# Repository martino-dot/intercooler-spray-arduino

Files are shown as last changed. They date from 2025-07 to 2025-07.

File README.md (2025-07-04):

# Intercooler Spray Arduino
A program for the Arduino Due that lets it control an intercooler sprayer in a Subaru STi. 

Intended setup is a developmental board on top of the Arduino to house a transistor that controls the incandescent bulb on the intercooler spray switch for feedback, and 3.3v relay board to control the pump. 

## Features
* Adjustable auto intercooler spray
* Can spray under boost, on a set interval, or manually
* Saves spray mode through power loss
* Cooldown spray
* Low water level warning and auto disable when level is low
* Refill detection and feedback
* Diagnostic features

## Required Dependencies
[DueFlashStorage](https://github.com/sebnil/DueFlashStorage)

## Pin Assignments
**Digital Pin 3** - Status LED Output (Linked to the Intercooler Spray Button Bulb)

**Digital Pin 5** -Low Level Sensor Input (Normally closed)

**Digital Pin 6** - Intercooler Spray Button Input (Or any other momentary button; Normally Open)

**Digital Pin 7** - HOBBs Switch Input (Used to determine if in boost; Normally Open)

**Digital Pin 8** -  Pump Relay Output

## Default parameters
**Single Button Press** - Whenever under boost, sprays for 2 seconds every 30 seconds. A cooldown spray is sprayed whenever car is under boost for more than 20 seconds in a 1 minute window.

**Double Button Press** - Sprays for 2 seconds every 30 seconds, regardless of boost. No boost tracking.

**Button Held Down** - If the button is held down for more than 2 seconds a *forced* spray will run, regardless of what mode it is in, until the button is let go. If water is low level, then this mode will NOT turn on and the status light will blink rapidly instead.

**Turning a Mode off** - Pressing the button **once** in a mode will turn it off.

**Switching Modes** - You **must** disable one of the modes before activating the other. 

**Additional Note** - Modes WILL be saved when the car is turned off and then back on. However, during startup delay, no mode will spray any water until it is done. If the water level is LOW then the mode will automatically be put into off.

**Startup Delay** - There is a 15 second delay before being able to control anything when turning the arduino/car on. During startup the status LED will blink once to signify for boost mode, blink twice for interval mode, and blink rapidly for low water, otherwise it will stay off.

**LED Status Blinks:**

&nbsp;&nbsp;1 Blink - Boost mode is ON

&nbsp;&nbsp;2 Blinks - Interval Mode is ON

&nbsp;&nbsp;3 Blinks - Mode 1 or 2 is turned off

&nbsp;&nbsp;5 Blinks - Tank Refilled

&nbsp;&nbsp;Rapid Blinks - Low Water Level

&nbsp;&nbsp;Constant On - Forced mode is running

## Diagnostics
When connected to the Arduino through the **programming USB port**, in serial console the following commands will report the following information:

&nbsp;&nbsp;**p** - Pump Relay Test (turns on pump for 1 second)

&nbsp;&nbsp;**l** - Status LED test (turns on LED for 1 second)

&nbsp;&nbsp;**w** - Checks water level

&nbsp;&nbsp;**m** - Lets you switch between modes (off, boost, and interval)

&nbsp;&nbsp;**d** - Reports current mode, time since last spray, and water status (Available after startup delay)

&nbsp;&nbsp;**r** - Restarts arduino

## 3D Models
I've included the 3D model for the intercooler box and intercooler box cap. It is designed to fit an Arduino Due, a single 3.3v relay module, and a development board on top of the arduino. The Arduino should sit on the side with the text engraved, so the programming USB port can be accessed when this is installed.

I WAS able to fit this box on top of the airbag control module in the center console of an 06 WRX, however I did not include the cap as it was a better fit without. Feel free to put this anywhere else.

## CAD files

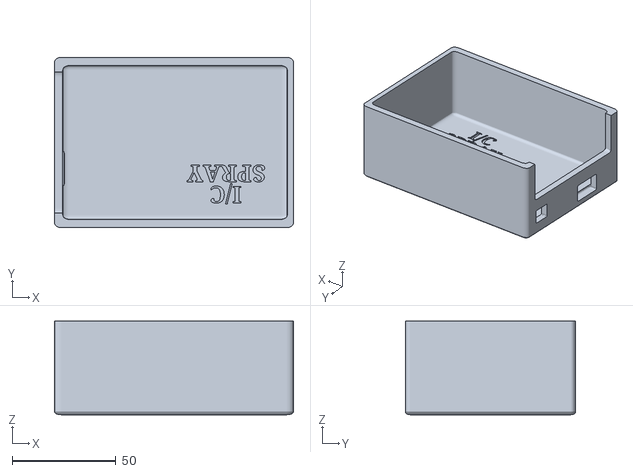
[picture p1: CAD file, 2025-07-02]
Intercooler Box.stl
115.0 x 82.0 x 45.0

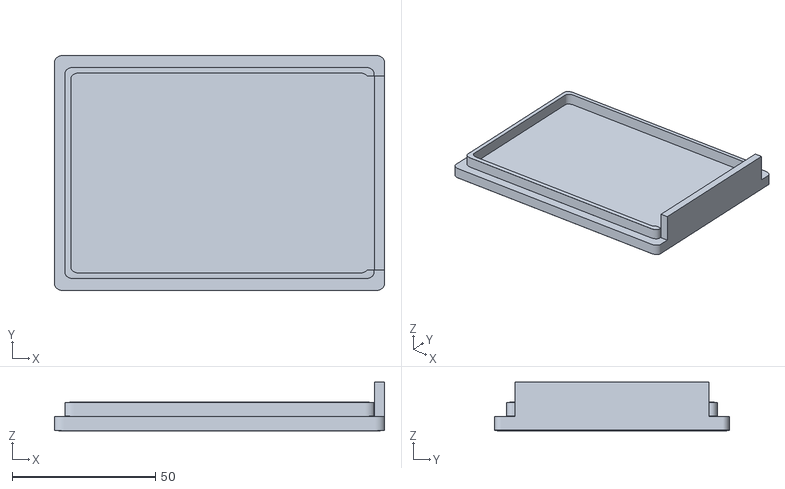
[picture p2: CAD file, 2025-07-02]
Intercooler Box Cap.stl
115.0 x 82.0 x 17.0

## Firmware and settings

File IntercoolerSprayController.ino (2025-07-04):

// === Intercooler Spray Controller with Arduino Due ===
// Inputs:
//   - Low water level sensor (digital, active LOW)
//   - Manual toggle button (momentary switch)
//   - HOBBS switch (digital, active HIGH when above boost threshold)
// Outputs:
//   - Pump relay (digital HIGH when spraying)
//   - Status LED (ON when spraying, BLINKS when water low)

#include <DueFlashStorage.h>
#include <DueTimer.h> 
DueFlashStorage dueFlashStorage;

// === Pin Assignments ===
const int lowLevelPin   = 5;   // Active LOW (NC sensor)
const int toggleButton  = 6;   // Momentary button, INPUT_PULLUP
const int hobbSwitchPin = 7;   // Active HIGH (NO switch)
const int pumpRelayPin  = 8;   // Output to pump relay
const int statusLEDPin  = 3;   // Status LED (incandescent)
// Pin 4 is open on terminal block

// === Constants ===
const uint32_t debounceDelay = 50;
const uint32_t holdThreshold = 2000;    // 2 sec hold for force mode
const uint32_t doubleClickMaxGap = 500; // max ms between clicks for double click

const uint32_t sprayDuration = 2000;    // ms
const uint32_t sprayInterval = 30000;   // ms

const uint32_t lowWaterBlinkDuration = 10000; // ms
const uint32_t startupDelay = 15000;  // ms delay before control
const uint32_t lowLevelDelay = 3000; // ms

const uint32_t waterStableTime = 1000;  // ms delay for water to "normalize"


// === Modes ===
enum Mode : uint8_t {
  MODE_OFF = 0,
  MODE_BOOST = 1,
  MODE_INTERVAL = 2,
  MODE_FORCE = 3
};

Mode currentMode = MODE_OFF;
Mode lastSavedMode = MODE_OFF;

// === Button State ===
bool lastButtonState       = HIGH;
uint32_t buttonPressStart  = 0;
bool buttonHeld            = false;
bool waitingForSecondClick = false;
uint32_t lastClickTime     = 0;
uint8_t clickCount         = 0;
uint32_t lastDebounceTime  = 0;
int      lastRawState      = HIGH;  
int      debouncedState    = HIGH; 

// === Spray State ===
bool spraying = false;
uint32_t sprayStartTime = 0;
uint32_t lastSprayTime = 0;

// === LED Blink State ===
bool ledState = false;
uint32_t lastBlinkTime = 0;
volatile bool flashActive = false;
volatile uint8_t flashCount = 0;
volatile uint8_t flashTotal = 0;
volatile uint32_t flashInterval = 0;
volatile uint32_t lastFlashTime = 0;

// === Low water warning ===
bool lowWaterWarningActive = false;
uint32_t lowWaterWarningStart = 0;
int      lastRawWater     = HIGH;           // last raw reading from sensor
int      lowWater   = HIGH;           // stable, debounced water level
uint32_t lastWaterChange  = 0;              // timestamp when water raw changed

// === Water Refill States ===
bool lastLowWaterState = true; // Assume last was LOW at startup
uint32_t refillDetectionTime = 0;
bool refillRecentlyDetected = false;

// === Startup timer ===
uint32_t startupTime = 0;
bool startupDone = false;

void setup() {
  Serial.begin(9600);
  
  pinMode(lowLevelPin, INPUT_PULLUP);
  pinMode(toggleButton, INPUT_PULLUP);
  pinMode(hobbSwitchPin, INPUT_PULLUP);
  pinMode(pumpRelayPin, OUTPUT);
  pinMode(statusLEDPin, OUTPUT);

  digitalWrite(pumpRelayPin, LOW);
  digitalWrite(statusLEDPin, LOW);

  // Read saved mode from flash storage
  uint8_t saved = dueFlashStorage.read(0);
  if (saved == MODE_BOOST || saved == MODE_INTERVAL) {
    currentMode = (Mode)saved;
    lastSavedMode = currentMode;
  } else {
    currentMode = MODE_OFF;
    lastSavedMode = MODE_OFF;
  }

  
  
  // Flash once for boost mode, twice for interval mode
  if (currentMode == MODE_BOOST) {
    startFlashPattern(1, 400);
  } else if (currentMode == MODE_INTERVAL) {
    startFlashPattern(2, 400);
  }

  startupTime = millis();
  startupDone = false;
}


void handleButton(uint32_t now, int reading) {

  // 1) track raw changes for debounce timing
  if (reading != lastRawState) {
    lastDebounceTime = now;
  }

  // 2) if stable beyond debounce interval, update debouncedState
  if (now - lastDebounceTime > debounceDelay) {
    if (reading != debouncedState) {
      debouncedState = reading;

      // on stable transition, handle press/release edges:
      if (debouncedState == LOW) {
        // falling edge: button pressed
        buttonPressStart = now;
        buttonHeld       = false;  // reset hold flag
        // Serial.println("button pressed");
      } else {
        // rising edge: button released
        if (!buttonHeld) {
          // handle quick click here (advance mode, etc.)
          //currentMode = (currentMode + 1) % NUM_MODES;
          //lastSavedMode = currentMode;
          //saveModeIfNeeded();
          clickCount++;
          if (!waitingForSecondClick) {
            waitingForSecondClick = true;
            lastClickTime = now;
          }
        } else {
          // was held & then released: revert to saved mode
          currentMode = lastSavedMode;
          stopSpray();
          Serial.println("button reverted");
        }
      }
    }

    // 3) check for hold event when stable LOW
    if (debouncedState == LOW && !buttonHeld && (now - buttonPressStart >= holdThreshold)) {
      buttonHeld  = true;
      currentMode = MODE_FORCE;
    }

    // Handle clicks after delay
    if (waitingForSecondClick && (now - lastClickTime > doubleClickMaxGap)) {
      // Single click
      if (clickCount == 1) {
        if (currentMode == MODE_OFF) {
          currentMode = MODE_BOOST;
          startFlashPattern(1, 250);
          saveModeIfNeeded();
          print("mode boost");
        } else if (currentMode == MODE_BOOST) {
          currentMode = MODE_OFF;
          startFlashPattern(3, 250);
          saveModeIfNeeded();
          print("mode off 1");
        } else if (currentMode == MODE_INTERVAL) {
          currentMode = MODE_OFF;
          startFlashPattern(3, 200);
          saveModeIfNeeded();
          print("mode off 2");
        }
        clickCount = 0;
        waitingForSecondClick = false;
      } else if (clickCount == 2) {
        // Only activate interval if no other mode active
        if (currentMode == MODE_OFF) {
          currentMode = MODE_INTERVAL;
          startFlashPattern(2, 400);
          saveModeIfNeeded();
          print("mode interval");
        }
        clickCount = 0;
        waitingForSecondClick = false;
      }

    }
  }

  // update raw state for next cycle
  lastRawState = reading;
}

inline void print(const char *msg) {
  Serial.println(msg);
}
inline void print(const String &msg) {
  Serial.println(msg);
}

void loop() {
  checkSerialBeforeStartup();
  
  uint32_t now = millis();

  bool rawWater = (digitalRead(lowLevelPin) != HIGH);     // LOW = low water (NC sensor)
  debouncedWaterLevel(now, rawWater);

  // Startup delay
  if (!startupDone) {
    // During startup delay, flash based on water & mode

    if ((now - startupTime >= lowLevelDelay) && lowWater) {
      flashLED(now, 200);
    }

    if (now - startupTime < startupDelay) {
      // digitalWrite(pumpRelayPin, LOW);
      return;
    }
    startupDone = true;
    digitalWrite(statusLEDPin, LOW);
  }

  // Read sensors
  bool underBoost = (digitalRead(hobbSwitchPin) == LOW); // LOW = boost (NO switch)
  bool buttonReading = (digitalRead(toggleButton));
  lastLowWaterState = lowWater;

  // Handle button with debounce and multiple clicks
  handleButton(now, buttonReading);

  // Low water warning: blink for 10s then shut off everything
  if (lowWater && !lowWaterWarningActive && currentMode != MODE_OFF) {
    lowWaterWarningActive = true;
    lowWaterWarningStart = now;
    currentMode = MODE_OFF;
    saveModeIfNeeded();
    stopSpray();
  }

  if (lowWaterWarningActive) {
    // Blink LED at 500ms rate
    if (now - lastBlinkTime >= 500) {
      ledState = !ledState;
      digitalWrite(statusLEDPin, ledState);
      lastBlinkTime = now;
    }
    // After 10s, turn off LED and modes
    if (now - lowWaterWarningStart >= lowWaterBlinkDuration) {
      digitalWrite(statusLEDPin, LOW);
      // currentMode = MODE_OFF; (already called)
      lowWaterWarningActive = false;
    }
    stopSpray();
    return;
  }

  // Force spray mode overrides everything else
  if (currentMode == MODE_FORCE) {
    if (!lowWater) {
      startSpray(now);
    } else {
      flashLED(now, 200);
    }
    return;
  }

  // Spray control based on mode
  switch (currentMode) {
    case MODE_BOOST:
      runBoostMode(now, underBoost);
      break;
    case MODE_INTERVAL:
      runIntervalMode(now);
      break;
    case MODE_OFF:
      stopSpray();
    default:
      break;
  }
  
  handleSerialDiagnostics();
  trackBoostDuration(underBoost, now);
  triggerCooldownSpray(now);
}

// Debounce water-level sensor (1s buffer)
void debouncedWaterLevel(uint32_t now, int raw) {
  if (raw != lastRawWater) {
    lastWaterChange = now;
    lastRawWater    = raw;
  }
  if (now - lastWaterChange >= waterStableTime) {
    lowWater = raw;
  }
}

// --- Spray Modes ---

void runBoostMode(uint32_t now, bool underBoost) {
  if (underBoost && !spraying && (now - lastSprayTime >= sprayInterval)) {
    startSpray(now);
  }
  if (spraying && (now - sprayStartTime >= sprayDuration)) {
    stopSpray();
  }
}

void runIntervalMode(uint32_t now) {
  if (!spraying && (now - lastSprayTime >= sprayInterval)) {
    startSpray(now);
  }
  if (spraying && (now - sprayStartTime >= sprayDuration)) {
    stopSpray();
  }
}

void startSpray(uint32_t now) {
  spraying = true;
  sprayStartTime = now;
  lastSprayTime = now;
  digitalWrite(pumpRelayPin, HIGH);
  digitalWrite(statusLEDPin, HIGH);
}

void stopSpray() {
  spraying = false;
  digitalWrite(pumpRelayPin, LOW);
  if (!flashActive) {
    digitalWrite(statusLEDPin, LOW);
  }
  
}

// --- LED Flash Patterns ---
void flashLED(uint32_t now, uint32_t interval) {
  if (now - lastBlinkTime >= interval) {
    ledState = !ledState;
    digitalWrite(statusLEDPin, ledState);
    lastBlinkTime = now;
  }
}

// Flash LED pattern count times with given on/off interval
// Called repeatedly from loop during startup or to signal mode
void startFlashPattern(uint8_t count, uint32_t interval) {
  Timer3.stop();                // stop it first
  Timer3.detachInterrupt();     // ensure it's clean

  flashTotal   = count * 2;  // on + off cycles
  flashCount   = 0;
  flashActive  = true;
  ledState = false;
  digitalWrite(statusLEDPin, LOW);
  Timer3.setPeriod(interval * 1000UL)
        .attachInterrupt(flashCallback)
        .start();
}

void flashCallback() {
  if (!flashActive) return;
  ledState = !ledState;
  digitalWrite(statusLEDPin, ledState);
  flashCount++;
  if (flashCount >= flashTotal) {
    flashActive = false;
    Timer3.stop();
    digitalWrite(statusLEDPin, LOW);
  }
}


// --- Flash Storage Save ---
void saveModeIfNeeded() {
  if (currentMode == MODE_BOOST || currentMode == MODE_INTERVAL || currentMode == MODE_OFF) {
    if (currentMode != lastSavedMode) {
      dueFlashStorage.write(0, currentMode);
      lastSavedMode = currentMode;
    }
  }
}

// === Serial Diagnostic Mode ===
void handleSerialDiagnostics() {
  if (Serial.available()) {
    char cmd = Serial.read();
    if (cmd == 'd') {
      Serial.println("=== Spray Controller Diagnostics ===");

      // Report current mode
      Serial.print("Mode: ");
      Serial.println(currentMode);

      // Report time since last spray
      Serial.print("Time since last spray: ");
      Serial.print((millis() - lastSprayTime) / 1000);
      Serial.println(" seconds");

      // Water status
      bool lowWater = lowWater;
      Serial.print("Water Level: ");
      Serial.println(lowWater ? "LOW" : "OK");
    }
  }
}

// === Cool-Down Spray Logic ===
// Track boost activity duration within a sliding time window
const uint32_t cooldownWindow = 60000; // 1 minute
const uint32_t boostThreshold = 20000; // 20 seconds in boost triggers cooldown
bool cooldownReady = false;
uint32_t boostTimeAccumulator = 0;
uint32_t lastBoostUpdate = 0;

void trackBoostDuration(bool underBoost, uint32_t now) {
  static bool lastBoost = false;

  if (currentMode != MODE_BOOST) return; // Skip tracking if interval mode is on

  if (underBoost) {
    if (!lastBoost) lastBoostUpdate = now;
    boostTimeAccumulator += now - lastBoostUpdate;
    lastBoostUpdate = now;
  } else {
    lastBoostUpdate = now;
  }

  if ((now - lastBoostUpdate) > cooldownWindow) {
    boostTimeAccumulator = 0;
  }

  if (boostTimeAccumulator >= boostThreshold) {
    cooldownReady = true;
    boostTimeAccumulator = 0; // Reset so it doesn’t re-trigger constantly
  }
  lastBoost = underBoost;
}

void triggerCooldownSpray(uint32_t now) {
  static bool cooling = false;
  static uint32_t cooldownStart = 0;

  if (currentMode != MODE_BOOST) return; // Skip cooldown spray if interval mode is on

  if (cooldownReady && !cooling && !lastLowWaterState) {
    startSpray(now);
    cooling = true;
    cooldownStart = now;
    cooldownReady = false;
  } else {
    return;
  }

  if (cooling && (now - cooldownStart >= sprayDuration)) {
    stopSpray();
    cooling = false;
  }
}

// === Refill Detection ===
void checkRefillDetection(uint32_t now) {
  bool currentLowWater = lowWater;

  // Detect transition from LOW to OK
  if (lastLowWaterState && !currentLowWater) {
    refillDetectionTime = now;
    refillRecentlyDetected = true;
    blinkLED(5, 100); // 5 quick blinks to acknowledge refill
  }

  // Clear flag after 5 seconds
  if (refillRecentlyDetected && (now - refillDetectionTime > 5000)) {
    refillRecentlyDetected = false;
  }

  lastLowWaterState = currentLowWater;
}

void blinkLED(uint8_t times, uint16_t duration) {
  for (uint8_t i = 0; i < times; i++) {
    digitalWrite(statusLEDPin, HIGH);
    delay(duration);
    digitalWrite(statusLEDPin, LOW);
    delay(duration);
  }
}

// === Diagnostic Relay Test & Mode Switch (before startup delay) ===
void checkSerialBeforeStartup() {
  if (Serial.available()) {
    char cmd = Serial.read();
    if (cmd == 'p') {
      Serial.println("Pump relay ON (test)");
      digitalWrite(pumpRelayPin, HIGH);
      delay(1000);
      digitalWrite(pumpRelayPin, LOW);
      Serial.println("Pump relay OFF");
    } else if (cmd == 'w') {
      Serial.print("Water Level: ");
      Serial.println(lowWater ? "LOW" : "OK");
    } else if (cmd == 'l') {
      Serial.println("LED ON (test)");
      digitalWrite(statusLEDPin, HIGH);
      delay(1000);
      digitalWrite(statusLEDPin, LOW);
      Serial.println("LED OFF");
    } else if (cmd == 'm') {
      Serial.println("Enter mode: 0=OFF, 1=BOOST, 2=INTERVAL");
      unsigned long startMs = millis();
      while (!Serial.available() && millis() - startMs < 10000) {
        
      }
      uint8_t newMode = Serial.parseInt();
      if (newMode <= 2) {
        currentMode = (Mode)newMode;
        saveModeIfNeeded();
        Serial.print("Mode set to ");
        Serial.println(currentMode);
      } else {
        Serial.println("Invalid mode");
      }
    } else if (cmd == 'r') {
      Serial.println("Resetting!");
      Serial.flush();
      NVIC_SystemReset();
    }
  }
}

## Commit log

2025-07-02 Add 3D Models
    [Intercooler Box Cap.stl, Intercooler Box.stl]
2025-07-04 Fix Status LED flashing
    [IntercoolerSprayController.ino]
